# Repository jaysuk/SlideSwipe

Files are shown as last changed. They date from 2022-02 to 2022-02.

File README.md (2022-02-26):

# SlideSwipe - Euclid Probe Edition
## Introduction
I liked the idea of the [SlideSwipe](https://github.com/chestwood96/SlideSwipe) method of deploying the probe but wanted to use an [Euclid Probe](https://euclidprobe.github.io/) so I have modified it to suit.
Taking probe             |  Stowing probe

## Pros and cons compared to SideSwipe
| Pro | Con |
| ---- | ---- |
| + Fully integrated | - Requires new cowling (and the accompanying rebuild of everything on it) |
| + Cables well hidden | - More complex (more parts, more steps) |
| + No loss in y area with the door closed |  |
| + Bed can't hit the arm |  |

## BOM
### Parts
- 1x MG90s Metal gear servo (the SG90 plastic gear ones work too but are not reccomended)
- 1x Euclid Probe Kit
- 1x 300mm servo extender cable (or make your own)
- 1x 1.5m of stranded wire with <1.2mm od (I tested 30awg silicone wire and 26awg ptfe wire)
- 3x 16mm piece of 4od2id PTFE tube (does not need to be the nice stuff)
- 1x 7mm piece of 4od2id PTFE tube (does not need to be the nice stuff) 
### Screws
- 7x M3x6 Socket head screw (cap head probably works too, one needs to be at least slightly attracted to magnets)
- 2x M3x8 Cap head screw
- 2x M3 nut

## Printing
All parts are designed to print in the orientation they come in and not require supports (If you have really bad overhang performance you can add a bit of support for the probe but it should not be necessary).

Designed to print in ABS at 0.4mm outer layer width and 0.2mm layer height.

I recommend ironing for the following parts, the rest can be printed without:
- Arm1
- Arm2
- ProbeCarrierTop
- ProbeCarrierBottom
- RailMountTop
- euclid mount

If you are going to do accents, I reccomend printing the following parts in the accent color:
- Arm1
- Arm2

## Cowling

This version uses the standard [Klicky Probe](https://github.com/jlas1/Klicky-Probe) cowling. I have also made a version of the klicky probe cowling for use with a mosquito.  

### Probe holder
Find the servo arm that fits the arm the best and cut off anything else on that arm if there is anything.
ArmServoArm
ArmServoArm2

Zero the servo (and check that it has at least over 90° of travel and isn't a continuously rotating one) and install the chosen arm, so it points a little over 90° when at the max point (picture is the max point).
ArmServoArm3

Pull the servo wire through the hole.
ArmServoMount

Insert the servo into the mount and fix it using 2 M3x6 screws
ArmServoMount2
ArmServoMount3
ArmServoMount4

Insert the short piece of PTFE in the left hole of "RailMountTop".
ArmServoMount5

Insert one of the longer pieces of ptfe into one of the holes of "Arm2"(the solid one).
Arm1

Put "Arm2" and "Arm1" onto the servo carrier like shown.
Arm2

Screw "RailMountTop" onto the servo carrier using 2 M3x6 screws.
Arm3

Put the other two longer pieces of ptfe into the remaining two holes in the arms.
Arm4

Put "ProbeCarrierTop" and "ProbeCarrierBottom" on the arms and screw them down using 2 M3x6 screws.
Arm5
Arm6

Add nuts in the pockets on the inside of the mount.
ArmNuts

That should be the physical build done.
Arm7

## Installation
### Installing the new cowling
The installation is the same as with the regular one, refer to the manual for that.

### Installing the probe arm
put the servo wire into the groove of the extrusion and tip the mount into it. Fix the assembly using the screws on the side.

Adjust the height to where it can grab the probe, but the arm does not hit the printhead then fix it in place.

Rout the servo wire through the slot in the front extrusion upwards into the slot of the top extrusion. The stock wire should be just long enough to pass through the panel though you'll probably have to remove the connector housing for that.

### Calibrating the servo angles
Using the servo command, find good values where the servo reliably hit the deployed and stowed position. The mechanism mechanically limits the travel but having the servo trying to push against it the whole time isn't great for it, so try to find some values that don't go way over the limits.

### Calibrating the pickup position
This should already be somewhat acurate but if it isn't find the pickup position and update the macro accordingly.

## Calibrate Z-Offset and start printing
Use your favourite method of calibrating the z-offet and start printing.

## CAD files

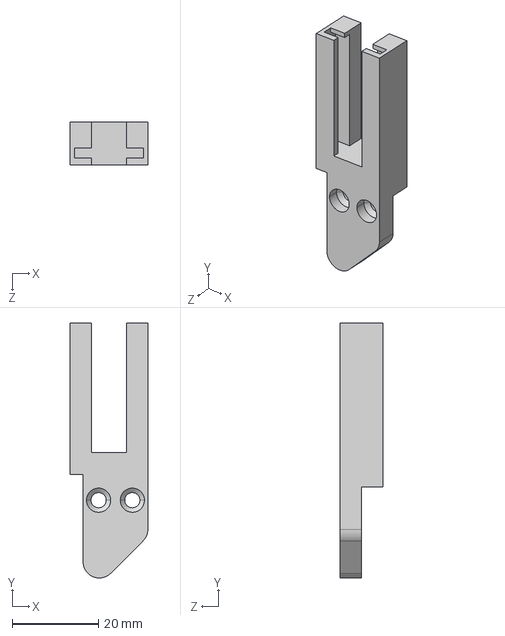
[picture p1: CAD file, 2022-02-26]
STEP/ProbeCarrierTop.step
18.0 x 59.0 x 10.0 mm

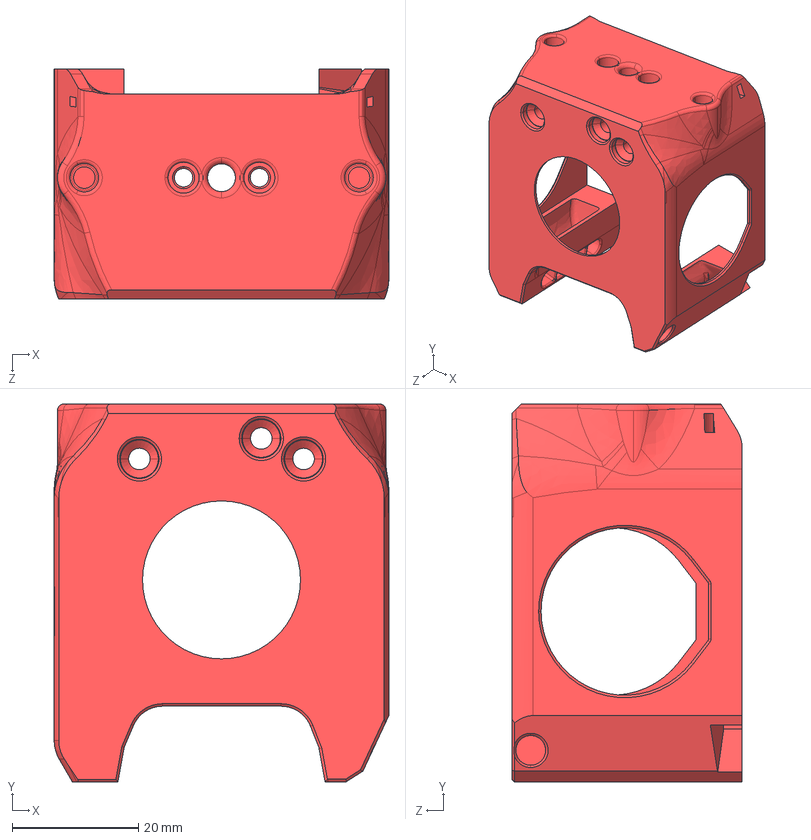
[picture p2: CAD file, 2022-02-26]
STEP/Mosquito_Cowling_wKlicky.STEP
53.0 x 59.9 x 36.5 mm

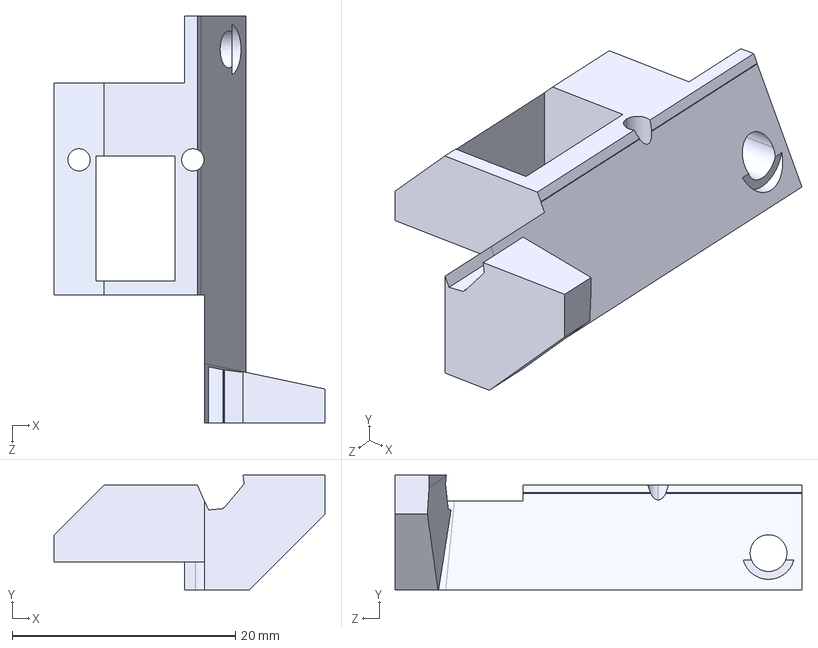
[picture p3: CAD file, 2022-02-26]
STEP/euclid mount.STEP
24.3 x 10.3 x 36.5 mm

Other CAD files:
STL/Mosquito_Cowling_wKlicky.STL
STL/ProbeCarrierTop.stl
STL/euclid mount.STL
